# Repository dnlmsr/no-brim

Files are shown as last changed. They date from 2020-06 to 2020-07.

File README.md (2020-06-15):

# no-brim

## Descrizione
Il progetto no-brim (no Barbaric Resizing Is Mandatory) è il progetto di una macchina in grado di realizzare lunghezze di tubi in PVC o altri materiali plastici definite dall'utente. L'intero sistema è basato sulla piattaforma open source Arduino MEGA che gestisce tutti gli input e gli output e le interazioni con l'utente.
## Autori
* [Daniele Moser](mailto:dnlmsr0@gmail.com)
* [Francesco Maraner](mailto:francesco.maraner@marconirovereto.it)
* [Michele Mattè](mailto:michele.matte@marconirovereto.it)

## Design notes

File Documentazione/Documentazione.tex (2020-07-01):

\documentclass{report}
\usepackage[utf8]{inputenc}
\usepackage[italian]{babel}
\usepackage{amsmath}
\usepackage{graphicx}
\usepackage{float}
\usepackage{pdfpages}
\usepackage{siunitx}
\usepackage{caption}
\usepackage{subcaption}
\usepackage{tikz}
\usetikzlibrary{shapes,arrows}

\DeclareSIUnit{\rpm}{rpm}
\sisetup{range-phrase=\div}

\title{Progetto no-brim}
\author{Daniele Moser, Francesco Maraner, Michele Mattè}

\begin{document}
\maketitle
\tableofcontents

\chapter{Introduzione}
no-brim è il progetto di una segatrice per tubi in PVC o altri materiali plastici, creato per il corso di Alta Formazione Professionale. Alla base di questo progetto, è presente la progettazione meccanica, elettronica e di programmazione di un macchinario semiautomatico per il taglio di lunghezza variabile di tubi mediante una discreta varietà di componenti (motori elettrici, assi, pistoni pneumatici, elettrovalvole, trasmissione a cinghia e lama circolare) che operano simultaneamente per realizzare il prodotto finale. Le motivazioni che ci hanno proiettato su questa tipologia di progetto derivano dal desiderio di mettere in atto le nozioni apprese durante il primo e secondo praticantato, dove ognuno dei 3 componenti del gruppo ha avuto modo di confrontarsi con il mondo del lavoro e di migliorare e accrescere le sue conoscenze nei vari ambiti in cui ha potuto lavorare, come la creazione di sistemi di trasmissione del moto o la programmazione.
\chapter{Meccanica}

\section{Descrizione macchina e motivazione dei componenti}
La parte meccanica, realizzata su Inventor, è stata divisa in 2 gruppi principali:
\begin{itemize}
\item Trasporto;
\item Taglio ed espulsione.
\end{itemize}

\subsection{Trasporto}
\begin{figure}[H]
  \centering
  \begin{subfigure}[H]{0.45\textwidth}
    \centering
    
  \end{subfigure}
  \hfill
  \begin{subfigure}[H]{0.45\textwidth}
    \centering
    
    \end{subfigure}
    \caption{Gruppo trasporto}
    \label{fig:vtcons}
\end{figure}
La prima parte si occupa del trasporto del tubo mediante un asse lineare ($l=\SI{300}{\mm}$) che sfrutta una trasmissione a vite a ricircolo di sfere, comandata da un motore elettrico, per spostare un pistone pneumatico (1M1), dove alla sua estremità è montata una lamiera che con la sua elasticità garantisce la corretta aderenza al tubo, sfruttando tutta la forza del pistone. Il pistone è stato collegato al pattino dell’asse lineare mediante una lamiera e una piastra. Dalla parte opposta all’asse, troviamo una lamiera a forma di “V” che garantisce il corretto scorrimento del tubo fino alla parte di taglio, grazie all’utilizzo di una rulliera costruita con dei cuscinetti a sfera.
Poco più a destra dell’asse lineare si colloca un altro pistone (2M1) fisso a telaio che si occupa di bloccare il tubo con la stessa logica del primo, contro un supporto in materiale tenero per non danneggiare l’oggetto da lavorare.
\begin{figure}[H]
  \centering
  
  \caption{Pistone bloccaggio}
  \label{fig:pinzaggio}
\end{figure}
All’estremità del telaio sono presenti delle lamiere che garantiscono il corretto ingresso ed uscita del tubo dalla parte di trasporto e dei sensori per controllare la posizione di quest’ultimo. Il telaio è stato realizzato mediante l’uso di tubolari quadrati in acciaio, dove sono stati fissati i supporti per le parti nominate in precedenza.

\subsection{Taglio ed espulsione}
\begin{figure}[H]
  \centering
  \begin{subfigure}[H]{0.45\textwidth}
    \centering
    
  \end{subfigure}
  \hfill
  \begin{subfigure}[H]{0.45\textwidth}
    \centering
    
    \end{subfigure}
    \caption{Gruppo taglio}
    \label{fig:vtcons}
\end{figure}
La seconda parte si occupa del taglio e l’espulsione del tubo mediante l’uso di una sega circolare ($D=\SI{300}{\mm}$) messa in moto da un motore elettrico monofase ($P = \SI{1,5}{\kW}$, $n_{max}=\SI{2500}{\rpm}$), il tutto collegato con una trasmissione a cinghie piatte con rapporto di trasmissione $i=\num{0.5}$ che si occupa di moltiplicare i giri della puleggia operatrice per garantire un taglio ottimale, come consigliato da tabella. Il sotto-assieme descritto è stato assemblato con un “telaietto” creato con dei tubolari quadrati in acciaio di piccole dimensioni per contenere il peso complessivo (motore, trasmissione, porta cuscinetto e lama) e vincolato ad un’estremità con 2 perni (che generano un effetto cerniera) che permettono la salita e la discesa di quest’ultimo mediante un pistone a doppio effetto (3MX). Per trasformare lo spostamento lineare del pistone in angolare dovuto alla rotazione attorno ai perni sono stati montati dei perni a forcella, collocati tra una piastra fissa e la base del pistone e tra l’estremità dello stelo e il telaietto, garantendo una buona spinta senza considerevoli perdite di forze. 

Infine, troviamo l’espulsione del pezzo lavorato grazie all’utilizzo di un pistone pneumatico (4M1) dove all’estremità dello stelo è stata fissata una lamiera con delle prolunghe laterali che fanno scorrere il tubo su un piano d’appoggio (con la possibilità di essere allungato in base alla lunghezza del tubo desiderata) verso una caduta libera.
\begin{figure}[H]
  \centering
  
  \caption{Pistone espulsione}
  \label{fig:espulsione}
\end{figure}
Il telaio portante è stato realizzato mediante l’uso di tubolari quadrati in acciaio, dove sono stati fissati i supporti per le parti nominate in precedenza.

\section{Calcoli di progetto}
\subsection{Calcolo dei giri utili del motore}
I tubi da tagliare, utilizzati per il trasporto di fluidi possono esseri creati con 3 diversi materiali plastici:
\begin{itemize}
\item PVC (cloruro di polivinile) con	$R_m = \SI{55}{\MPa}$;
\item PVC-C $R_m = \SI{60}{\MPa}$;
\item PE (polietilene) $R_m = \SI{17}{\MPa}$;
\item PP (polipropilene) $R_m = \SI{35}{\MPa}$.
\end{itemize}
PVC, PE e PP fanno parte della famiglia dei pannelli termoplastici (tabella $V_t$ consigliate) dove la velocità di taglio $V_t$ consigliata si aggira tra $\SIrange{50}{75}{\m\per\s}$ e l’avanzamento tra $\SIrange{0.05}{0.1}{\mm\per\s}$.

\begin{figure}[H]
    \centering
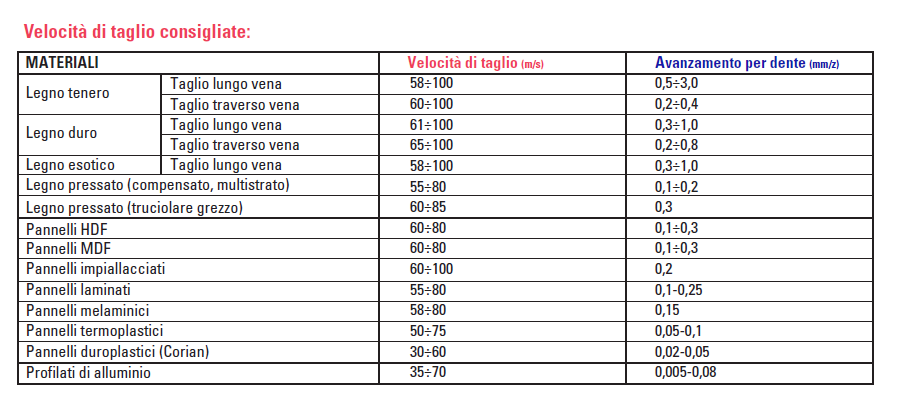
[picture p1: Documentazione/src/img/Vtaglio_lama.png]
    
    \caption{$V_t$ consigliate}
    \label{fig:vtcons}
\end{figure}

Seguendo la linea nera (per materiali plastici) della tabella, si assume un diametro della lama circolare di $D=\SI{300}{\mm}$ (inoltre utilizzata nella maggior parte dei casi, grazie al suo ottimo rapporto efficienza/ingombro).

\begin{figure}[H]
    \centering
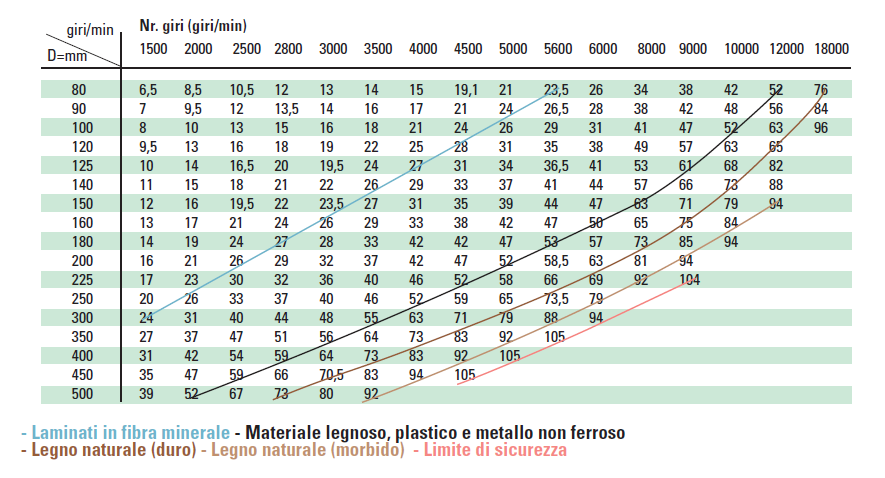
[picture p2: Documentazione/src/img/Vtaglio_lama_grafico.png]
    
    \caption{Grafico $V_t$ consigliate}
    \label{fig:grafvtcons}
\end{figure}

Conoscendo la $V_t$ richiesta dal materiale per essere tagliato possiamo calcolare il numero di giri generati dal motore, che successivamente verranno moltiplicati mediante una trasmissione a cinghie piatte.
Sapendo che:
\begin{equation}
  \omega=\frac{V_t}{r_{lama}}
\end{equation}
Si calcola:
\begin{itemize}
\item $\omega_{min} = \frac{V_t}{r} = \frac{\SI{50}{\m\per\s}}{\SI{0,15}{\m}} = \SI{334}{\radian\per\s} $;
\item $\omega_{max}  = \frac{V_t}{r}= \frac{75}{0,15} = \SI{500}{\radian\per\s}$.
\end{itemize}

Per una lettura più comoda si converte la $\omega$ in rpm mediante la seguente formula:
\begin{equation}
  n = \frac{60\omega}{2\pi}
\end{equation}

Quindi:
\begin{description}
\item $n_{min} = \frac{334\cdot 60}{2\pi} \approx \SI{3200}{\rpm}$;
\item $n_{max} = \frac{500\cdot 60}{2\pi} \approx \SI{4800}{\rpm}$.
\end{description}

Conoscendo questi dati, con l’intenzione di utilizzare una trasmissione a cinghie piatte con un rapporto di trasmissione $i = \num{0,5}$ (che moltiplica la velocità della puleggia operatrice del doppio rispetto a quella motrice) si può restringere il campo di ricerca del motore monofase fino a \SI{2500}{\rpm} massimi che, grazie alla trasmissione, potrà raggiungere i \SI{5000}{\rpm}.

\subsection{Calcolo della forza di taglio}
La taglia del tubo da tagliare, nel nostro caso, ha le seguenti dimensioni:
\begin{description}
\item $D = \SI{104}{\mm}$
\item $d = \SI{100}{\mm}$
\item $A = \SI{641}{\mm\squared}$
\end{description}

Utilizzando il carico di rottura del materiale più resistente (PVC-C) con $\sigma = \SI{60}{\MPa}$, si calcola la sua $\tau$, sapendo che $\tau = \frac{\sigma}{\sqrt{3}}$ e di conseguenza $\tau = k\frac{F}{A}$ dove per sezioni circolari $k=4/3$. Rovesciando la formula si può calcolare la $F$ necessaria per tagliare il tubo:

\begin{equation}
\tau=\frac{60}{\sqrt{3}} = \SI{35}{\MPa}
\end{equation}
\begin{equation}
F = \frac{A\tau}{k} = \SI{16,7}{\kN}
\end{equation}

\subsection{Calcolo della potenza del motore}
Per il calcolo della potenza del motore, dopo aver trovato il numero di giri necessari, è stato utilizzato il metodo sperimentale. Grazie alla presenza di una sega circolare (da falegnameria) e il tubo da lavorare, dopo varie prove e tagli siamo giunti alla conclusione di adottare un motore con una potenza di \SI{1,5}{\kW}. La possibilità di provare il taglio ci ha permesso di stabilire le seguenti considerazioni:
\begin{itemize}
\item Le velocità di taglio, calcolate in precedenza sono state del tutto coerenti con le prove effettuate.
\item La velocità di avanzamento, invece, ha soddisfatto le aspettative con un andamento lento e costante, senza imprimere troppa forza (circa \SI{50}{\N}) tra il tubo e la lama per evitare che quest'ultima si bloccasse.
  \end{itemize}
  \subsection{Dimensionamento della trasmissione}
  \begin{figure}[H]
    \centering
    \begin{subfigure}[H]{0.45\textwidth}
    \centering
    
  \end{subfigure}
  \hfill
  \begin{subfigure}[H]{0.45\textwidth}
    \centering
    
    \end{subfigure}
    \caption{Gruppo trasmissione}
    \label{fig:vtcons}
\end{figure}
Le cinghie sono organi flessibili impiegati nella trasmissione di potenza da una puleggia motrice a una condotta, montate su alberi disposti ad una certa distanza (interasse). Le cinghie possono appartenere a due gruppi distinti: cinghie di tipo convenzionale e cinghie sincrone.
Le cinghie di tipo convenzionale trasmettono il moto sfruttando l’aderenza (attrito) con il profilo esterno della puleggia. In questo caso possono verificarsi scorrimenti fra la cinghia e la puleggia durante il moto.
Le cinghie sincrone trasmettono il moto tramite l’ingranamento dei denti della cinghia con quelli della puleggia. Non sono soggette a scorrimento e necessitano di un precarico molto modesto.
Industrialmente sono usate cinghie piatte, trapezoidali e sincrone.
Per dimensionare una trasmissione partiamo dai dati del motore, forniti dal datasheet:

\begin{table}[H]
\centering
\begin{tabular}{|l|c|}
\hline
\multicolumn{2}{|c|}{\textbf{Dati motore}} \\ \hline
Potenza & \SI{1,5}{\kW} \\ \hline
Giri motore & \SI{2500}{\rpm} \\ \hline
Diametro albero & \SI{19}{\mm} \\ \hline
\end{tabular}
\end{table}

Successivamente, una volta trovato il numero di giri che vogliamo sviluppare sull’operatrice ($n=\SI{5000}{\rpm}$), calcolo il rapporto di trasmissione ($i$) e l’interasse ($I$) tra i due elementi rotanti in base alla dimensione delle mie pulegge, che assumo a piacere dalla serie di Renard R20 a partire da un diametro minimo di \SI{40}{\mm}.

Assumiamo il diametro della puleggia motrice $D_m=\SI{100}{\mm}$ e di conseguenza (per rispettare il rapporto di trasmissione e la serie R20) $D_o=\SI{50}{\mm}$ per il diametro dell’operatrice. Questa scelta è giustificata dagli ingombri in fase di modellazione 3D per tagliare correttamente il tubo senza urti.
Il calcolo dell’interasse dipende dal carico, nel nostro caso $I\geq 3\cdot D_m$ per trasmissioni a carico variabile. Una volta rispettata questa condizione si può scegliere a piacimento la lunghezza in base alle esigenze (ingombri, etc...)

\begin{table}[H]
\centering
\resizebox{\textwidth}{!}{
\begin{tabular}{|l|c|l|}
\hline
\multicolumn{2}{|c|}{\textbf{Dati Pulegge}} & \multicolumn{1}{c|}{\textbf{Formula}} \\ \hline
Numero giri motrice ($n_m$) & \SI{2500}{\rpm} & Fornito dal motore \\ \hline
Numero giri operatrice ($n_o$) & \SI{5000}{\rpm} & $\frac{n_m}{i}$ \\ \hline
Rapporto di trasmissione ($i$) & \num{0,5} & $\frac{n_m}{n_o}$ \\ \hline
Diametro puleggia motrice ($D_m$) & \SI{100}{\mm} & Scelta personale rispettando R20 \\ \hline
Diametro puleggia operatrice ($D_o$) & \SI{50}{\mm} & $D_o=D_m\cdot i$ \\ \hline
Interasse ($I$) & \SI{300}{\mm} & $I=3\cdot D_m$ \\ \hline
\end{tabular}
}
\end{table}

Durante la progettazione di una trasmissione è importante consultare le tabelle unificate che forniscono dati di correzione in base ai materiali utilizzati per la realizzazione e il servizio che devono compiere.
Dati provenienti dalle tabelle del manuale di Meccanica:
\begin{table}[H]
\centering
\begin{tabular}{|c|c|l|}
\hline
\multicolumn{2}{|c|}{\textbf{Dati tabelle}} & \multicolumn{1}{c|}{\textbf{Provenienza dati}} \\ \hline
$F_s$ & \num{1,2} & Tab. I.101 Fattore di servizio \\ \hline
$F_t$ & \num{1} & Tab. I.102 Fattore correttivo \\ \hline
$F_\alpha$ & \num{1} & Tab. I.108 Coeff. correzione \\ \hline
$P_1$ & \num{0,7} & Tab. I.106 P specifica (cinghia gomma-tessile) \\ \hline
\end{tabular}
\end{table}

\subsubsection{Calcolo della potenza corretta}
\begin{equation}
P_c=P\cdot F_s\cdot F_t
\end{equation}
Dove $P$ è la potenza erogata dal motore, $F_s=\num{1,2}$ da tabella per macchine utensili che lavorano dalle 8 alle 10 ore al giorno e $F_t=1$ da tabella per condizioni normali.
\begin{equation}
P_c = \SI{1,5}{\kW}\cdot \num{1,2}\cdot 1 = \SI{1,8}{\kW}
\end{equation}
\subsection{Calcolo della velocità periferica della puleggia minore}
\begin{equation}
  V = \frac{\pi D_{min}n_{min}}{\num{60000}}
\end{equation}
Dove $D_{min}=D_o$ e $n_{min}=n_o$.
\begin{equation}
V=\frac{\pi\cdot 50\cdot 5000}{\num{60000}} = \SI{13,1}{\m\per\s}
\end{equation}

\subsubsection{Calcolo della lunghezza della cinghia}
\begin{equation}
  l=2I+\frac{\pi (D_m+D_o)}{2}+\frac{(D_o-D_m)^2}{4I}=\SI{838}{\mm}\approx\SI{840}{\mm}
\end{equation}
Si approssima a \SI{840}{\mm} per lasciare un po' di gioco prima di tendere o allentare la cinghia.

\subsubsection{Calcolo dell’angolo di avvolgimento $\alpha$}
\begin{equation}
  \alpha = \SI{180}{\degree}-\SI{57}{\degree}\cdot\frac{D_m-D_o}{I}=\SI{190}{\degree}
\end{equation}
Il valore servirà per trovare $F\alpha$ da tabella.
\subsubsection{Calcolo della larghezza della cinghia $a$}
I principali materiali utilizzati per la costruzione di cinghie piatte sono:
\begin{itemize}
\item cuoio;
\item struttura composita di laminati plastici e gomme o resine;
\item struttura composita di gomme e tessili;
\item cotone, balata e altre fibre tessili vegetali;
\item gomma o materiali plastici (per alte velocità).
\end{itemize}
Da questa informazione si può calcolare la larghezza della cinghia ricavando il valore $P_1$ in base al materiale scelto, nel nostro caso gomma-tessile pesante in cotone a 4 tele, data la seguente formula:
\begin{equation}
  a = \frac{P_c}{P_1F_\alpha}=\frac{\SI{1,8}{\cm}}{\SI{0,7}{\cm}\cdot 1} = \SI{2,57}{\cm}\approx\SI{26}{\mm}
\end{equation}
La larghezza della cinghia è stata scelta in riferimento ai valori dati dalla serie R40, a partire dal valore minimo di 16 mm.

\subsubsection{Calcolo dello spessore della cinghia $s$}
Dalla seguente tabella ricavo lo spessore $s$ della cinghia in base al materiale scelto in precedenza. In questo caso \SI{6}{\mm}.
\begin{table}[H]
\resizebox{\textwidth}{!}{%
\begin{tabular}{|c|c|c|c|c|}
\hline
\multicolumn{5}{|c|}{\textbf{Campo applicazione per cinghie piatte}} \\ \hline
\textit{\textbf{\begin{tabular}[c]{@{}c@{}}Tipo di cinghia \\ e materiale\end{tabular}}} & \textit{\textbf{Costruzione}} & \textit{\textbf{\begin{tabular}[c]{@{}c@{}}Potenza Max \\ $[\si{\kW}]$\end{tabular}}} & \textit{\textbf{\begin{tabular}[c]{@{}c@{}}Velocità Max \\ $[\si{\m\per\s}]$\end{tabular}}} & \textit{\textbf{\begin{tabular}[c]{@{}c@{}}Spessore cinghia s \\ $[\si{\mm}]$\end{tabular}}} \\ \hline
Cuoio & \begin{tabular}[c]{@{}c@{}}- Semplice\\ - Doppia\\ - Triplice\end{tabular} & \begin{tabular}[c]{@{}c@{}}750\\ 500\\ 1500\end{tabular} & \begin{tabular}[c]{@{}c@{}}40\\ 30\\ 25\end{tabular} & \begin{tabular}[c]{@{}c@{}}4 - 6\\ 7 - 9\\ 11 - 14\end{tabular} \\ \hline
\begin{tabular}[c]{@{}c@{}}Componente:\\ - Nylon\\ - Poliestere\end{tabular} & \begin{tabular}[c]{@{}c@{}}- Lamina in gomma\\ - Plastici\end{tabular} & 3500 & 40 & 0,5 - 6 \\ \hline
\begin{tabular}[c]{@{}c@{}}Composita:\\ - Gomma\\ - Tessile\end{tabular} & \begin{tabular}[c]{@{}c@{}}- Tessuti medi\\ - Tessuti pesanti\end{tabular} & \begin{tabular}[c]{@{}c@{}}750\\ 1500\end{tabular} & \begin{tabular}[c]{@{}c@{}}40\\ 40\end{tabular} & \begin{tabular}[c]{@{}c@{}}6 - 20\\ 6 - 20\end{tabular} \\ \hline
  \begin{tabular}[c]{@{}c@{}}Cotone, balata \\ e altre fibre tessili\end{tabular} & \begin{tabular}[c]{@{}c@{}}- Multistrato\\ - Unico strato\end{tabular} & 1500 & 30 & 4 -
                                                                                                                                                                         20 \\ \hline
\begin{tabular}[c]{@{}c@{}}In gomma e plastici \\ per alte velocità\end{tabular} & - Unico strato & 50 & 70 & 0,5 - 2 \\ \hline
\end{tabular}%
}
\caption{Parametri consigliati per vari tipi di cinghie}
\end{table}
\subsubsection{Calcolo della larghezza della puleggia $b$}
\begin{equation}
  b = \num{1,15}\cdot a\approx\SI{30}{\mm}
\end{equation}
\subsubsection{Calcolo della bombatura della puleggia $h$}
Le pulegge per cinghie piatte vengono costruite con profilo esterno leggermente bombato per ottenere la stabilità della cinghia sulla corona. I materiali più indicati sono l’alluminio, per il peso contenuto, o la ghisa per piccole serie.
\begin{equation}
 h=\num{0,006}\cdot b=\SI{0.186}{\mm}
\end{equation}
\section{Schema elettro-pneumatico}
\subsection{Scelta dei componenti}
Lo schema elettro-pneumatico è stato realizzato con i seguenti componenti:
\begin{description}
\item[Compressore] Si occupa di accumulare e innalzare la pressione dell’aria all’interno del suo serbatoio per alimentare il circuito pneumatico;
\item[Gruppo trattamento aria] Composta da filtro di scarico manuale, un riduttore di pressione variabile, un manometro e una valvola di sicurezza (quasi sempre inclusa nei gruppi trattamento aria industriali per togliere aria al sistema in caso di emergenza);
\item[Pistone pinza mobile 1M1, pistone pinza fissa 2M1, pistone espulsore 4M1] Composti dalla stessa logica, tramite l'uso di:
  \begin{itemize}
  \item 1 pistone a singolo effetto con ritorno a molla con le seguenti caratteristiche: corsa di \SI{50}{\mm}, diametro pistone \SI{16}{\mm} e forza di spinta teorica a $\SI{6}{\bar}$ di $F=\SIrange{90}{120}{\bar}$ (dove la sola andata è utile per svolgere il lavoro richiesto di bloccaggio ed espulsione);
  \item 1 strozzatore che si utilizza solamente uno strozzatore senza una o più valvole di non ritorno perché la regolazione della portata mediante strozzatura su ambedue i lati viene spesso applicata in cilindri a semplice effetto o in cilindri di piccole dimensioni che svolgono lavori “semplici”. Quest’aspetto inoltre va a vantaggio dei costi di realizzazione dell’impianto e della semplicità d’applicazione;
  \item 1 valvola 3/2 normalmente chiusa comandata elettricamente nella fase di spinta e con ritorno a molla;
  \end{itemize}
\item[Pistone sollevamento lama circolare 3MX] Composto da:
  \begin{itemize}
  \item 1 pistone a doppio effetto con le seguenti caratteristiche: corsa \SI{100}{\mm}, diametro del pistone \SI{32}{\mm} e forza di spinta teorica a \SI{6}{\bar} di $F=\SIrange{415}{483}{\N}$, dati necessari a soddisfare il corretto movimento della lama verso l'alto, considerando che il peso che deve movimentare è composto dal telaietto con relativa trasmissione (motore, cinghia, pulegge etc) che risulta essere circa \SI{25}{\kg}, di conseguenza \SI{250}{\N} con un ulteriore aggiunta di \SI{50}{\N} per la fase di avanzamento come descritto nei calcoli. In questo modo, con una determinata forza richiesta ($F=\SI{300}{\N}$) è stato scelto un pistone leggermente sovradimensionato per tenere conto delle possibili piccole perdite di forza dovute agli attriti dei perni a forcella;
  \item 2 strozzatori in scarico per ottenere una buona regolazione della portata, entro certi limiti indipendenti dal carico applicato allo stelo, poiché viene guidato dal cuscino d’aria che si forma nella camera di scarico; agendo sulle viti di regolazione degli strozzatori si possono tarare separatamente le velocità delle due corse.
  \item 1 valvola 5/3 a centri chiusi comandata elettricamente con ritorno a molla in ambedue i versi di commutazione per comandare il pistone a doppio effetto. La scelta di questa valvola è dovuta alla necessità di mantenere in posizione la lama (senza spostarsi in punti indesiderate, evitando danni all’oggetto da tagliare) in caso di arresto voluto o improvviso.
  \end{itemize}

\item[Finecorsa dei pistoni] Festo prevede l’utilizzo di sensori magneti che determinano la corsa dello stelo, montati direttamente sul cilindro.
\end{description}

\subsection{Lista componenti}
\begin{table}[H]
\centering
\begin{tabular}{|l|c|}
  \hline
  {\textbf{Componenti}} & \textbf{Quantità} \\ \hline
  Pistone singolo effetto & 3 \\ \hline
  Pistone doppio effetto & 1 \\ \hline
  Elettrovalvola 3/2 nc con ritorno a molla & 3 \\ \hline
  Elettrovalvola 5/3 centri chiusi con ritorno a molla & 1 \\ \hline
  Strozzatori & 5 \\ \hline
  Valvole di non ritorno & 2 \\ \hline
  Gruppo trattamento aria & 1 \\ \hline
  Compressore & 1 \\ \hline
\end{tabular}
\end{table}

\chapter{Elettronica}

\section{Descrizione circuiti e motivazione dei componenti}
La parte elettronica, realizzata utilizzando KiCad e DesignSpark Eletrical, è stata suddivisa in 2 parti separate:
\begin{itemize}
\item PCB
\item Quadro
\end{itemize}
\section{PCB}
La prima parte è costituita da una serie di circuiti che permettono ad Arduino di comandare 4 elettrovalvole e due motori rispettivamente da 24V e da 230V. Nel caso specifico viene inserito tra l'output di Arduino e l'elettrovalvola, un MOSFET che fungerà da interruttore per alimentare e disalimentare l'elettrovalvola in questione o il motore.
\begin{figure}[H]
  \centering
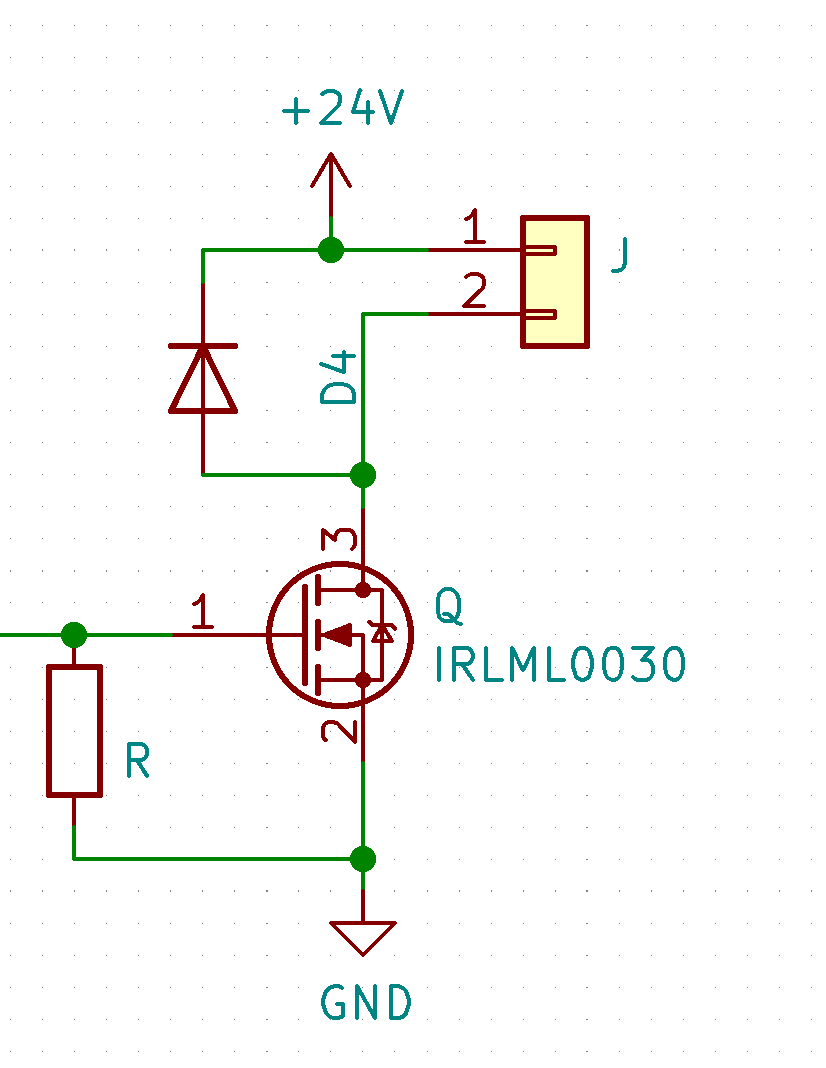
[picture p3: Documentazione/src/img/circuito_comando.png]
  
  \caption{Circuito di comando}
  \label{fig:circuito}
\end{figure}
Per quanto riguarda le dimensioni del circuito stampato risultano contenute nonostante la quantità di dispositivi ad esso collegati, infatti il circuito integra solamente la parte composta da una morsettiera con 10 connettori, dedicati ad ognuno degli ingressi necessari, i circuiti di comando e i morsetti di uscita. Ogni circuito di comando è composto un MOSFET e un diodo: 
\begin{description}
\item[Diodo] La funzione del diodo in questo circuito è quella di proteggere il MOSFET e l'uscita di Arduino da sovratensioni indesiderate provocate dagli avvolgimenti presenti nelle elettrovalvole e nei motori, in alcuni casi viene inserito anche per evitare le inversioni di tensione. Per quanto riguarda il circuito di comando per il motore della lama monofase $\SI{230}{\volt}$, utilizzato per la sega, si è preferito introdurre anche un relè così da permettere di utilizzare un MOSFET con corrente di sollecitazione minore e ridurre la tensione massima presente sulla scheda da $\SI{230}{\volt}$ AC a $\SI{24}{\volt}$ DC.
\item[MOSFET] È il cuore del circuito infatti, grazie ad una piccola sollecitazione ($\SIrange{0}{10}{\milli\ampere}$) riesce a veicolare correnti di valore molto più alte ($\SIrange{1}{7}{\ampere}$), nel nostro caso le correnti non superano normalmente i $\SI{2}{\ampere}$ quindi, date le correnti basse non necessitano della presenza di alette di raffreddamento. Per quanto riguarda invece il motore responsabile della movimentazione dell'asse lineare necessita di $\SI{7,7}{\ampere}$ come corrente di spunto.
\end{description}
\section{Quadro}
La seconda parte del circuito è racchiusa in un quadretto di modeste dimensioni al quale viene data in ingresso una tensione monofase $\SI{230}{\volt}$ e in uscita due tensioni continue dal valore di $\SI{24}{\volt}$ e $\SI{12}{\volt}$.
Per permettere la conversione in tensione continua sono stati creati due circuiti di trasformazione separati e provvisti di interruttori magnetotermici differenziali per garantire la sicurezza elettrica del quadro.
Il quadretto in questione verrà in seguito collegato al connettore di terra dello stabilimento.
\section{Descrizione della componentistica}
Sono stati utilizzati i seguenti componenti:
\begin{itemize}
\item Motore dell'asse lineare: un motore brushless di Pamoco con dati di targa di $\SI{24}{\volt}$ e corrente di spunto di $\SI{7,7}{\ampere}$;
\item Motore della sega circolare: un motore di Bonfiglioli con dati di targa di $\SI{230}{\volt}$ monofase e corrente di spunto di $\SI{2,4}{\ampere}$;;
\item Elettrovalvola 4/2 di Fluidmec con pilotaggio elettrico su entrambi i lati con dati di targa di $\SI{24}{\volt}$ e corrente di spunto di $\SI{0,8}{\ampere}$; 
\item Elettrovalvola 5/3 di Festo a centri chiusi con pilotaggio elettrico su entrambi i lati con dati di targa di $\SI{24}{\volt}$ e corrente di spunto di $\SI{0,5}{\ampere}$;
\item Elettrovalvola 3/2 di Schmieranlagen con pilotaggio elettrico a sinistra e ritorno a molla a destra con dati di targa di $\SI{24}{\volt}$ e corrente di spunto di $\SI{0,8}{\ampere}$;
\end{itemize} 

\chapter{Programmazione}
\section{Programma Arduino}
L'intero sistema è basato sulla piattaforma open source \emph{Arduino MEGA}, la quale gestisce l'intero funzionamento del sistema. Il programma che gira su Arduino è basato su un sistema a task e scheduler, ciò vuol dire che l'intero programma è suddiviso in piccoli sottoprogrammi (task) che vengono eseguiti ad una certa frequenza predefinita dallo scheduler il quale compito è appunto quello di eseguire questi programmi al momento giusto. Il programma dispone anche di un sistema per verificare se il sistema è real-time, ovvero che la capacità di calcolo del microcontrollore sia adeguata alla mole di calcoli richiesti dal programma. Questo sistema verifica appunto la saturazione della CPU.
\subsection{SFC}
Il programma per la movimentazione viene eseguito da un task adibito al corretto funzionamento dove si è cercato di replicare un sistema a stati.
\begin{enumerate}
\item Stato di STOP;
\item Tutte le movimentazioni vengono calibrate, quindi tutti i pistoni tranne 2M1 vengono resettati e l'asse lineare si sposta nella posizione più lontana dalla lama;
\item Viene pinzato il tubo con il pistone 1M1;
\item Viene resettato il pistone 2M1 e l'asse lineare si sposta in avanti verso la lama. Se la lunghezza del tubo non è soddisfatta si torna al punto 2;
\item Il tubo viene pinzato con il pistone 2M1;
\item Viene accesa la lama e viene effettuato il taglio con 3M1;
\item Viene fermata la lama e viene retratto il blocco di taglio con 3M2;
\item Viene espulso il pezzo finito e si torna allo stato di calibrazione.
\end{enumerate}
\section{Sistema asse lineare}
È stato deciso di studiare in profondità il funzionamento dell'asse lineare per poter tarare con maggior accuratezza il controllore. È quindi necessario conoscere le specifiche sia del motore che dell'asse lineare:
\begin{table}[H]
\centering
\begin{tabular}{|l|c|c|}
  \hline
\textbf{Descrizione}    & \textbf{Sigla} & \textbf{Valore}   \\ \hline
  \multicolumn{3}{|c|}{\textbf{Dati Motore}}                                                               \\ \hline

Corrente di spunto      & $i_s$                              & \SI{7,7}{\ampere}                       \\ \hline
Tensione nominale       & $v_n$                              & \SI{24}{\volt}                          \\ \hline
Velocità motore a vuoto & $\omega_{n}$                       & \SI{3500}{\rpm}                          \\ \hline
\multicolumn{3}{|c|}{\textbf{Dati asse lineare}}                                                         \\ \hline
Momento di inerzia      & $J$                                & \SI{0,11}{\kg\cm\squared\per\m} \\ \hline
Passo vite              & $p$                                & \SI{5}{\mm}                         \\  \hline
\end{tabular}
\end{table}
È necessario inoltre calcolare la resistenza di armatura e la costante elettrica e meccanica del motore:
\begin{equation}
  R_a=\frac{v_n}{i_s}=\SI{3,12}{\ohm}
\end{equation}
\begin{equation}
  K=\frac{v_n}{\omega_n}=\SI{6,86}{\milli\volt\per\rpm}
\end{equation}
\subsection{Sistema motore}
Per poter studiare il motore si fa uso delle formule del motore in corrente continua:
\begin{equation}
  \begin{cases}
    Ri(t)+K\omega(t)=V(t)\\
    J\dot \omega(t)=Ki(t)
  \end{cases}
\end{equation}
Si decide quindi di portare l'intero sistema nel dominio di Laplace:
\begin{equation}
  \begin{cases}
    RI(s)+K\omega(s)=V(s)\\
    Js\omega(s)=KI(s)    
  \end{cases}
\end{equation}
Eliminando $I(s)$ si ottiene:
\begin{equation}
  \frac{Js\omega(s)}{K}=\frac{V(s)-K\omega(s)}{R}\longrightarrow\frac{\omega(s)}{V(s)}=\frac{K}{JsR+K^2}
\end{equation}
\subsection{Sistema completo}
Dopo aver trovato la funzione che descrive il funzionamento del motore CC è necessario anche descrivere il funzionamento del controllore. Nel nostro caso è stato utilizzato un controllore PID. Lo schema a blocchi rappresenta il sistema completo:
\begin{figure}[H]
  \centering
  \begin{tikzpicture}[auto, node distance=3cm,>=latex']
    \tikzstyle{block} = [draw, rectangle, 
    minimum height=3em, minimum width=6em]
    \tikzstyle{sum} = [draw, circle, node distance=1cm]
    \tikzstyle{input} = [coordinate, node distance=1cm]
    \tikzstyle{output} = [coordinate, node distance=2cm]
    \tikzstyle{pinstyle} = [pin edge={to-,thin,black}]
    
    \node [input, name=input] {};
    \node [sum, right of=input] (sum){};
    \node [block, right of=sum] (controller) {Controller};
    \node [block, right of=controller] (motore) {Motore};
    \node [block, right of=motore] (conversione) {Conversione};
    \node [output, right of=conversione] (output) {};

    \draw [draw,->] (input) -- node {$S_p$} (sum);
    \draw [->] (sum) -- node {$e$} (controller);
    \draw [->] (controller) -- (motore);
    \draw [->] (motore) -- (conversione);
    \draw [->] (conversione) -- node [name=y] {$y$}(output);
    \draw [->] (y) |- (5,-2) -| (sum);
    \node [below left] at (sum) {$-$};
  \end{tikzpicture}
\end{figure}
A questo punto avendo la descrizione del sistema completo si è deciso di simulare l'intero sistema tramite l'utilizzo di Octave. Il risultato sottostante si è ottenuto con $K_P=2$ e $K_I=K_D=0$.
\begin{figure}[H]
  \centering
  
  \caption{Simulazione asse lineare}
  \label{fig:simulazione}
\end{figure}
Tarando quindi i giusti valori di PID è possibile ottenere un sistema teoricamente ottimale, ma che richiede comunque una prova sperimentale sul campo.

\chapter{Sviluppi futuri}
\section{Sviluppi ambito elettronico}
  Uno sviluppo futuro per questo progetto consisterebbe nella progettazione e realizzazione di un circuito di sicurezza implementando barriere o cancelli che impediscano agli operatori di infortunarsi a causa delle diverse parti in movimento presenti nel macchinario.

\section{Sviluppi ambito programmazione} 
Sono da implementare l'interfacciamento con l'utente tramite l'utilizzo di un encoder e di un display LCD, nonché la comunicazione seriale con un PC per effettuare un debugging del sistema se necessario. Un'implementazione futura potrebbe consistere nella creazione di un applicativo di visione, magari per il controllo della qualità la deformazione del tubo dopo il taglio.
  
\section{Sviluppi ambito meccanico}  
  Un altra possibile modifica al progetto potrebbe consistere nella creazione di un sistema mobile per quanto riguarda la struttura contenente la sega circolare così da permettere anche quest'ultima di muoversi al posto della sola movimentazione del tubo, ottimizzando così le tempistiche dedicate al taglio.
  Un possibile miglioramento futuro, riferito alla parte meccanica, potrebbe consistere nell’utilizzo di una struttura verticale con la lamiera di supporto per lo scorrimento del tubo a forma di “V”, con relativa rulliera e i pistoni 1M1 e 2M1 (che utilizzano lo stesso sistema di trasporto) disposti al di sopra di quest’ultima. Per la parte di taglio, invece, si pensava di effettuare il taglio mediante una lama circolare calettata ad un piccolo motore elettrico, il tutto fissato a delle piastre montate su un corsoio con relative sicurezze, per movimentare agevolmente un peso contenuto in orizzontale; ed infine per la parte di scarico una lamiera mobile che viene mossa da un pistone per rilasciare il pezzo finito lungo uno scivolo.

\chapter{Crediti}
\section{Software utilizzati}
\begin{description}
\item[Autodesk Inventor]Per la realizzazione e la rappresentazione dei pezzi meccanici
  \item[Fluidsim]Per la progettazione del sistema pneumatico
\item[KiCad]Per la progettazione del PCB
\item[Arduino]Per la programmazione del sistema
\item[Octave]Per la simulazione del sistema
\item[\LaTeX]Per la documentazione
\end{description}
\includepdf[pages=-,angle=90]{src/Tavole/completo.pdf}
\includepdf[pages=-,angle=90]{src/Tavole/trasporto.pdf}
\includepdf[pages=-,angle=90]{src/Tavole/taglio_1.pdf}
\includepdf[pages=-,angle=90]{src/Tavole/trasmissione.pdf}
\includepdf[pages=-]{src/img/impianto_elettropneumatico.pdf}
\end{document}

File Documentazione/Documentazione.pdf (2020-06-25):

# Progetto no-brim

Daniele Moser, Francesco Maraner, Michele Matt`e

25 giugno 2020

# Indice

1 Introduzione | 2
2 Meccanica | 3
2.2.5 | Calcolo della velocit`a periferica della puleggia minore . . | 8

1

# Capitolo 1

# Introduzione

2

# Capitolo 2

# Meccanica

## 2.1 Descrizione macchina e motivazione dei componenti

La parte meccanica, realizzata su Inventor, `e stata divisa in 2 gruppi principali:

- Trasporto;
- Taglio ed espulsione.

### 2.1.1 Trasporto

La prima parte si occupa del trasporto del tubo mediante un asse lineare (l = 300 mm) che sfrutta una trasmissione a vite a ricircolo di sfere, comandata da un motore elettrico, per spostare un pistone pneumatico (1M1), dove alla sua estremit`a `e montata una lamiera che con la sua elasticit`a garantisce la corretta aderenza al tubo, sfruttando tutta la forza del pistone. Il pistone `e stato collegato al pattino dell’asse lineare mediante una lamiera e una piastra. Dalla parte opposta all’asse, troviamo una lamiera a forma di “V” che garantisce il corretto scorrimento del tubo fino alla parte di taglio, grazie all’utilizzo di una rulliera costruita con dei cuscinetti a sfera. Poco pi`u a destra dell’asse lineare si colloca un altro pistone (2M1) fisso a telaio che si occupa di bloccare il tubo con la stessa logica del primo, contro un supporto in materiale tenero per non danneggiare l’oggetto da lavorare. All’estremit`a del telaio sono presenti delle lamiere che garantiscono il corretto ingresso ed uscita del tubo dalla parte di trasporto e dei sensori per controllare la posizione di quest’ultimo. Il telaio `e stato realizzato mediante l’uso di tubolari quadrati in acciaio, dove sono stati fissati i supporti per le parti nominate in precedenza.

3

### 2.1.2 Taglio ed espulsione

La seconda parte si occupa del taglio e l’espulsione del tubo mediante l’uso di una sega circolare (D = 300 mm) messa in moto da un motore elettrico monofase (P = 1.5 kW, nmax = 2500 rpm), il tutto collegato con una trasmissione a cinghie piatte con rapporto di trasmissione i = 0.5 che si occupa di moltiplicare i giri della puleggia operatrice per garantire un taglio ottimale, come consigliato da tabella. Il sottoassieme descritto `e stato assemblato con un “telaietto” creato con dei tubolari quadrati in acciaio di piccole dimensioni per contenere il peso complessivo (motore, trasmissione, porta cuscinetto e lama) e vincolato ad un’estremit`a con 2 perni (che generano un effetto cerniera) che permettono la salita e la discesa di quest’ultimo mediante un pistone a doppio effetto (3MX). Per trasformare lo spostamento lineare del pistone in angolare dovuto alla rotazione attorno ai perni sono stati montati dei perni a forcella, collocati tra una piastra fissa e la base del pistone e tra l’estremit`a dello stelo e il telaietto, garantendo una buona spinta senza considerevoli perdite di forze.
Infine, troviamo l’espulsione del pezzo lavorato grazie all’utilizzo di un pistone pneumatico (4M1) dove all’estremit`a dello stelo `e stata fissata una lamiera con delle prolunghe laterali che fanno scorrere il tubo su un piano d’appoggio (con la possibilit`a di essere allungato in base alla lunghezza del tubo desiderata) verso una caduta libera. Il telaio portante `e stato realizzato mediante l’uso di tubolari quadrati in acciaio, dove sono stati fissati i supporti per le parti nominate in precedenza.

## 2.2 Calcoli di progetto

### 2.2.1 Calcolo dei giri utili del motore

I tubi da tagliare, utilizzati per il trasporto di fluidi possono esseri creati con 3 diversi materiali plastici:

- PVC (cloruro di polivinile) con Rm = 55 MPa;
- PVC-C Rm = 60 MPa;
- PE (polietilene) Rm = 17 MPa;
- PP (polipropilene) Rm = 35 MPa.

PVC, PE e PP fanno parte della famiglia dei pannelli termoplastici (tabella Vt consigliate) dove la velocit`a di taglio Vt consigliata si aggira tra 50 m s⁻¹ ÷ 75 m s⁻¹

e l’avanzamento tra 0.05 mm s⁻¹ ÷ 0.1 mm s⁻¹

4


Figura 2.1: Vt consigliate

Seguendo la linea nera (per materiali plastici) della tabella, si assume un diametro della lama circolare di D = 300 mm (inoltre utilizzata nella maggior parte dei casi, grazie al suo ottimo rapporto efficienza/ingombro).


Figura 2.2: Grafico Vt consigliate

Conoscendo la Vt richiesta dal materiale per essere tagliato possiamo calcolare il numero di giri generati dal motore, che successivamente verranno moltiplicati mediante una trasmissione a cinghie piatte. Sapendo che:

ω =

Vt

rlama

(2.1)

Si calcola:

5

- ωmin =

Vt
r =

50 m s⁻¹
0.15 m = 334 rad s⁻¹
;
- ωmax =

Vt
r =

75

0,15 = 500 rad s⁻¹

Per una lettura pi`u comoda si converte la ω in rpm mediante la seguente formula:
n =

60ω
2π

(2.2)

Quindi:

nmin =

334·60
2π ≈ 3200 rpm;

nmax =

500·60
2π ≈ 4800 rpm.

Conoscendo questi dati, con l’intenzione di utilizzare una trasmissione a cinghie piatte con un rapporto di trasmissione i = 0.5 (che moltiplica la velocit`a della puleggia operatrice del doppio rispetto a quella motrice) si pu`o restringere il campo di ricerca del motore monofase fino a 2500 rpm massimi che, grazie alla trasmissione, potr`a raggiungere i 5000 rpm.

### 2.2.2 Calcolo della forza di taglio

La taglia del tubo da tagliare, nel nostro caso, ha le seguenti dimensioni:

D = 104 mm

d = 100 mm

A = 641 mm²

Utilizzando il carico di rottura del materiale pi`u resistente (PVC-C) con σ = 60 MPa, si calcola la sua τ , sapendo che τ = √σ
3

e di conseguenza τ = k

F
A
dove per sezioni circolari k = 4/3. Rovesciando la formula si pu`o calcolare la F necessaria per tagliare il tubo:

τ =

60
√
3
= 35 MPa | (2.3)

F =

Aτ
k
= 16.7 kN | (2.4)

### 2.2.3 Calcolo della potenza del motore

Per il calcolo della potenza del motore, dopo aver trovato il numero di giri necessari, `e stato utilizzato il metodo sperimentale. Grazie alla presenza di una sega circolare (da falegnameria) e il tubo da lavorare, dopo varie prove e tagli siamo giunti alla conclusione di adottare un motore con una potenza di 1.5 kW. La possibilit`a di provare il taglio ci ha permesso di stabilire le seguenti considerazioni:

6

- Le velocit`a di taglio, calcolate in precedenza sono state del tutto coerenti con le prove effettuate.
- La velocit`a di avanzamento, invece, ha soddisfatto le aspettative con un andamento lento e costante, senza imprimere troppa forza (circa 50 N) tra il tubo e la lama per evitare che quest’ultima si bloccasse.

### 2.2.4 Dimensionamento della trasmissione

Le cinghie sono organi flessibili impiegati nella trasmissione di potenza da una puleggia motrice a una condotta, montate su alberi disposti ad una certa distanza (interasse). Le cinghie possono appartenere a due gruppi distinti: cinghie di tipo convenzionale e cinghie sincrone. Le cinghie di tipo convenzionale trasmettono il moto sfruttando l’aderenza (attrito) con il profilo esterno della puleggia. In questo caso possono verificarsi scorrimenti fra la cinghia e la puleggia durante il moto. Le cinghie sincrone trasmettono il moto tramite l’ingranamento dei denti della cinghia con quelli della puleggia. Non sono soggette a scorrimento e necessitano di un precarico molto modesto. Industrialmente sono usate cinghie piatte, trapezoidali e sincrone. Per dimensionare una trasmissione partiamo dai dati del motore, forniti dal datasheet:

Dati motore
Potenza | 1.5 kW
Giri motore | 2500 rpm
Diametro albero | 19 mm

Successivamente, una volta trovato il numero di giri che vogliamo sviluppare sull’operatrice (n = 5000 rpm), calcolo il rapporto di trasmissione (i) e l’interasse
(I) tra i due elementi rotanti in base alla dimensione delle mie pulegge, che assumo a piacere dalla serie di Renard R20 a partire da un diametro minimo di 40 mm.
Assumiamo il diametro della puleggia motrice Dm = 100 mm e di conseguenza (per rispettare il rapporto di trasmissione e la serie R20) Do = 50 mm per il diametro dell’operatrice. Questa scelta `e giustificata dagli ingombri in fase di modellazione 3D per tagliare correttamente il tubo senza urti. Il calcolo dell’interasse dipende dal carico, nel nostro caso I ≥ 3 · Dm per trasmissioni a carico variabile. Una volta rispettata questa condizione si pu`o scegliere a piacimento la lunghezza in base alle esigenze (ingombri, etc...)
Dati Pulegge | Formula
Numero giri motrice (nm) | 2500 rpm | Fornito dal motore
Numero giri operatrice (no) | 5000 rpm | nm i
Rapporto di trasmissione (i) | 0.5 | nm no
Diametro puleggia motrice (Dm) | 100 mm | Scelta personale rispettando R20
Diametro puleggia operatrice (Do) | 50 mm | Do = Dm · i
Interasse (I) | 300 mm | I = 3 · Dm

7

Durante la progettazione di una trasmissione `e importante consultare le tabelle unificate che forniscono dati di correzione in base ai materiali utilizzati per la realizzazione e il servizio che devono compiere. Dati provenienti dalle tabelle del manuale di Meccanica:

Dati tabelle | Provenienza dati
Fs | 1.2 | Tab. I.101 Fattore di servizio
Ft | 1 | Tab. I.102 Fattore correttivo
Fα | 1 | Tab. I.108 Coeff. correzione
P1 | 0.7 | Tab. I.106 P specifica (cinghia gomma-tessile)

Calcolo della potenza corretta

Pc = P · Fs · Ft | (2.5)

Dove P `e la potenza erogata dal motore, Fs = 1.2 da tabella per macchine utensili che lavorano dalle 8 alle 10 ore al giorno e Ft = 1 da tabella per condizioni normali.
Pc = 1.5 kW · 1.2 · 1 = 1.8 kW | (2.6)

### 2.2.5 Calcolo della velocit`a periferica della puleggia mino-

re

V =

πDminnmin 60 000 | (2.7)

Dove Dmin = Do e nmin = no.

V =

π · 50 · 5000 60 000
= 13.1 m s⁻¹ | (2.8)

Calcolo della lunghezza della cinghia

l = 2I +

π(Dm + Do)
2

+

(Do − Dm)

2
4I

= 838 mm ≈ 840 mm (2.9)

Si approssima a 840 mm per lasciare un po’ di gioco prima di tendere o allentare la cinghia.

Calcolo dell’angolo di avvolgimento α

α = 180◦ − 57◦
·

Dm − Do I
= 190◦ | (2.10)

Il valore servir`a per trovare F α da tabella.

8

Calcolo della larghezza della cinghia a

I principali materiali utilizzati per la costruzione di cinghie piatte sono:

- cuoio;
- struttura composita di laminati plastici e gomme o resine;
- struttura composita di gomme e tessili;
- cotone, balata e altre fibre tessili vegetali;
- gomma o materiali plastici (per alte velocit`a).

Da questa informazione si pu`o calcolare la larghezza della cinghia ricavando il valore P1 in base al materiale scelto, nel nostro caso gomma-tessile pesante in cotone a 4 tele, data la seguente formula:

a =

Pc
P1Fα

=

1.8 cm
0.7 cm · 1
= 2.57 cm ≈ 26 mm | (2.11)

La larghezza della cinghia `e stata scelta in riferimento ai valori dati dalla serie R40, a partire dal valore minimo di 16 mm.

Calcolo dello spessore della cinghia s

Dalla seguente tabella ricavo lo spessore s della cinghia in base al materiale scelto in precedenza. In questo caso 6 mm.

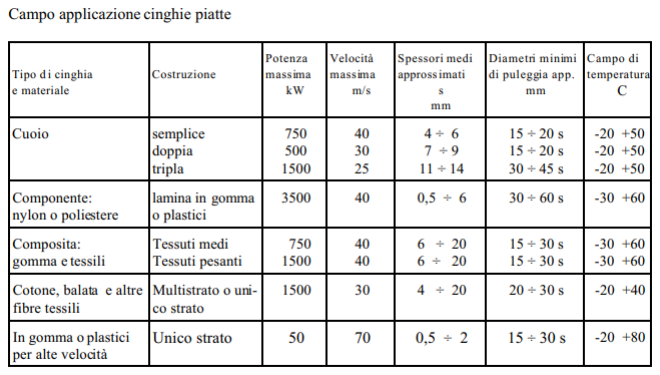
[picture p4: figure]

Figura 2.3: Parametri consigliati per vari tipi di cinghie

9

Calcolo della larghezza della puleggia b

b = a1.15 ≈ 30 mm | (2.12)

Calcolo della bombatura della puleggia h

Le pulegge per cinghie piatte vengono costruite con profilo esterno leggermente bombato per ottenere la stabilit`a della cinghia sulla corona. I materiali pi`u indicati sono l’alluminio, per il peso contenuto, o la ghisa per piccole serie.

h = b0.006 = 0.186 mm | (2.13)

## 2.3 Schema elettropneumatico

### 2.3.1 Scelta dei componenti

Lo schema elettropneumatico `e stato realizzato con i seguenti componenti:

Compressore Si occupa di accumulare e innalzare la pressione dell’aria all’interno del suo serbatoio per alimentare il circuito pneumatico;

Gruppo trattamento aria Composta da filtro di scarico manuale, un riduttore di pressione variabile, un manometro e una valvola di sicurezza (quasi sempre inclusa nei gruppi trattamento aria industriali per togliere aria al sistema in caso di emergenza);

Pistone pinza mobile 1M1, pistone pinza fissa 2M1, pistone espulsore 4M1 Composti dalla stessa logica, tramite l’uso di:

- 1 pistone a singolo effetto con ritorno a molla con le seguenti caratteristiche: corsa di 50 mm, diametro pistone 16 mm e forza di spinta teorica a 6 bar di F = 90 bar ÷ 120 bar (dove la sola andata `e utile per svolgere il lavoro richiesto di bloccaggio ed espulsione);
- 1 strozzatore che si utilizza solamente uno strozzatore senza una o pi`u valvole di non ritorno perch´e la regolazione della portata mediante strozzatura su ambedue i lati viene spesso applicata in cilindri a semplice effetto o in cilindri di piccole dimensioni che svolgono lavori “semplici”. Quest’aspetto inoltre va a vantaggio dei costi di realizzazione dell’impianto e della semplicit`a d’applicazione;
- 1 valvola 3/2 normalmente chiusa comandata elettricamente nella fase di spinta e con ritorno a molla;

Pistone sollevamento lama circolare 3MX Composto da:

- 1 pistone a doppio effetto con le seguenti caratteristiche: corsa 100 mm, diametro del pistone 32 mm e forza di spinta teorica a 6 bar di F = 415 N÷483 N, dati necessari a soddisfare il corretto movimento della lama verso l’alto, considerando che il peso che deve movimentare `e

10 composto dal telaietto con relativa trasmissione (motore, cinghia, pulegge etc) che risulta essere circa 25 kg, di conseguenza 250 N con un ulteriore aggiunta di 50 N per la fase di avanzamento come descritto nei calcoli. In questo modo, con una determinata forza richiesta (F = 300 N) `e stato scelto un pistone leggermente sovradimensionato per tenere conto delle possibili piccole perdite di forza dovute agli attriti dei perni a forcella;
- 2 strozzatori in scarico per ottenere una buona regolazione della portata, entro certi limiti indipendenti dal carico applicato allo stelo, poich´e viene guidato dal cuscino d’aria che si forma nella camera di scarico; agendo sulle viti di regolazione degli strozzatori si possono tarare separatamente le velocit`a delle due corse.
- 1 valvola 5/3 a centri chiusi comandata elettricamente con ritorno a molla in ambedue i versi di commutazione per comandare il pistone a doppio effetto. La scelta di questa valvola `e dovuta alla necessit`a di mantenere in posizione la lama (senza spostarsi in punti indesiderate, evitando danni all’oggetto da tagliare) in caso di arresto voluto o improvviso.

Finecorsa dei pistoni Festo prevede l’utilizzo di sensori magneti che determinano la corsa dello stelo, montati direttamente sul cilindro.

### 2.3.2 Lista componenti

Componenti | Quantit`a
Pistone sing. effetto | 3
Pistone doppio effetto | 1
Elettrovalvola 3/2 nc con ritorno a molla | 3
Elettrovalvola 5/3 centri chiusi con ritorno a molla | 1
Strozzatori | 5
Valvole di non ritorno | 2
Gruppo trattamento aria | 1
Compressore | 1

11

## 2.4 Elettronica

## 2.5 Programmazione

## 2.6 Utilizzo della macchina

## 2.7 Sviluppi futuri

## 2.8 Crediti

12

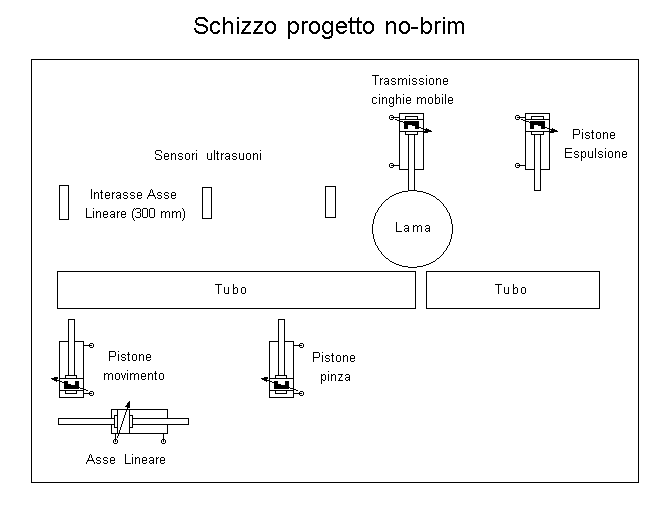
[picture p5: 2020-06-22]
Documentazione/src/img/schizzo_progetto.png

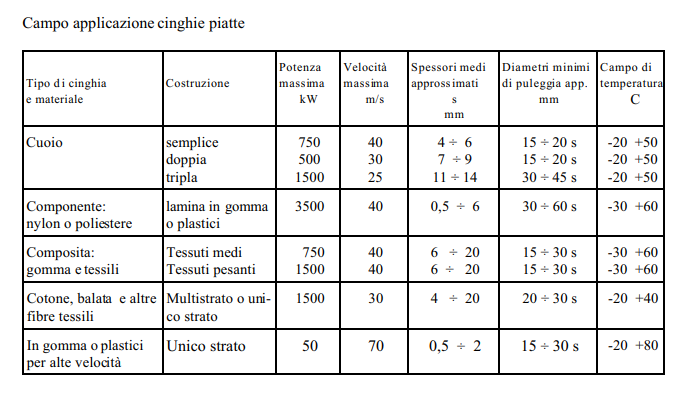
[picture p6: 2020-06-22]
Documentazione/src/img/tabella_cinghie.png

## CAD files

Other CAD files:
Quadro/Sinottico Cablaggio.dwg
Quadro/Copertina.dwg
Quadro/Schema Elettrico.dwg
Meccanica/Progetto Inventor no-brim/Assiemi/Assieme 1 - Trasporto.iam
Meccanica/Progetto Inventor no-brim/Assiemi/Assieme 2 - Taglio.iam
Meccanica/Progetto Inventor no-brim/Assiemi/Assieme completo - Trasporto Taglio.iam
Meccanica/Progetto Inventor no-brim/Assiemi/Lamiere e sensore ultrasuoni - Trasporto.iam
Meccanica/Progetto Inventor no-brim/Assiemi/Pistone scarico - Taglio.iam
Meccanica/Progetto Inventor no-brim/Assiemi/Pistoni pinza - Trasporto.iam
Meccanica/Progetto Inventor no-brim/Assiemi/Rulliera - Trasporto.iam
Meccanica/Progetto Inventor no-brim/Assiemi/Supporto saldato pistone 2 - Trasporto.iam
Meccanica/Progetto Inventor no-brim/Assiemi/Telaietto trasmissione - Taglio.iam
Meccanica/Progetto Inventor no-brim/Assiemi/Telaio - Taglio.iam
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

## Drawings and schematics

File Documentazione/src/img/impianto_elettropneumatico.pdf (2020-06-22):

## IMPIANTO ELETTROPNEUMATICO no-brim

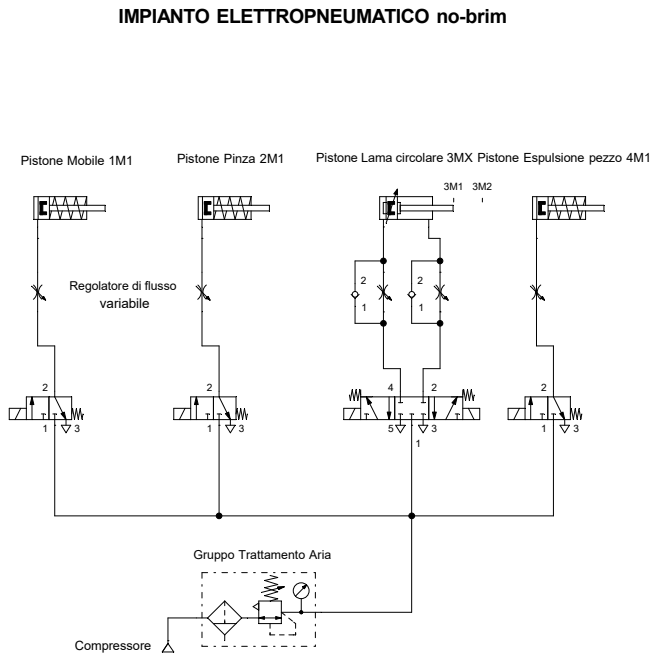
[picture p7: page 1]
Pistone Mobile 1M1; Pistone Pinza 2M1; Pistone Lama circolare 3MX Pistone Espulsione pezzo 4M1; Compressore

Regolatore di flusso
variabile

Gruppo Trattamento Aria

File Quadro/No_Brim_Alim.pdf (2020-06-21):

1 | 2 | 3 | 4 | 5 | 6 | 7 | 8 | 9 | 10
0 | 21/06/2020 | Utente DesignSpark Electrical | -X1 1

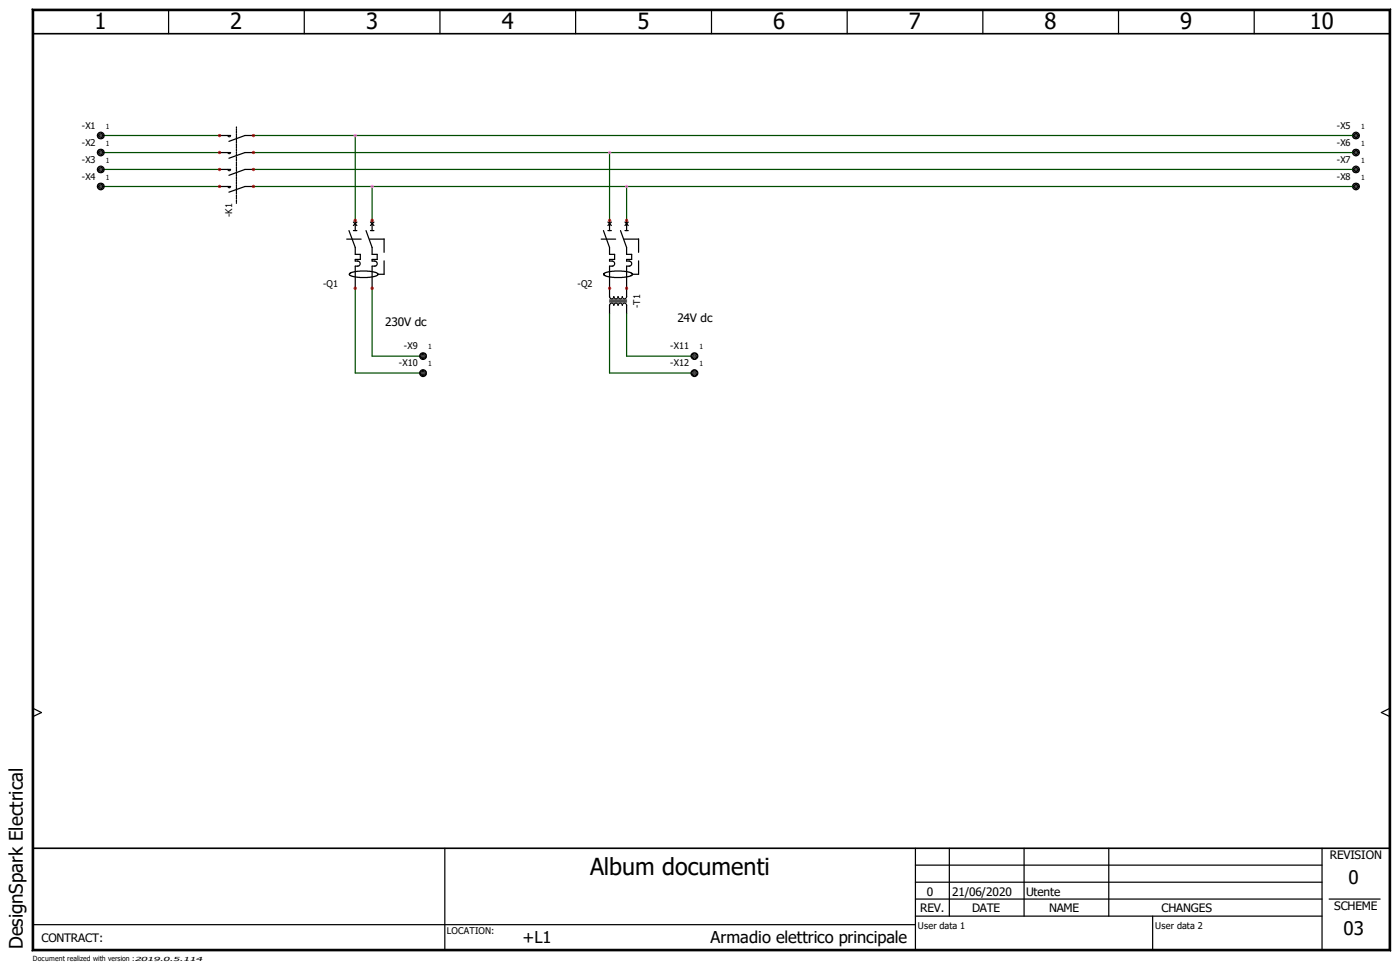
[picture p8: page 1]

Album documenti | REVISION 0 SCHEME

REV. | DATE | NAME | CHANGES

2019.0.5.114 | Armadio elettrico principale LOCATION: Document realized with version : CONTRACT:

User data 1 | User data 2 | 03 +L1

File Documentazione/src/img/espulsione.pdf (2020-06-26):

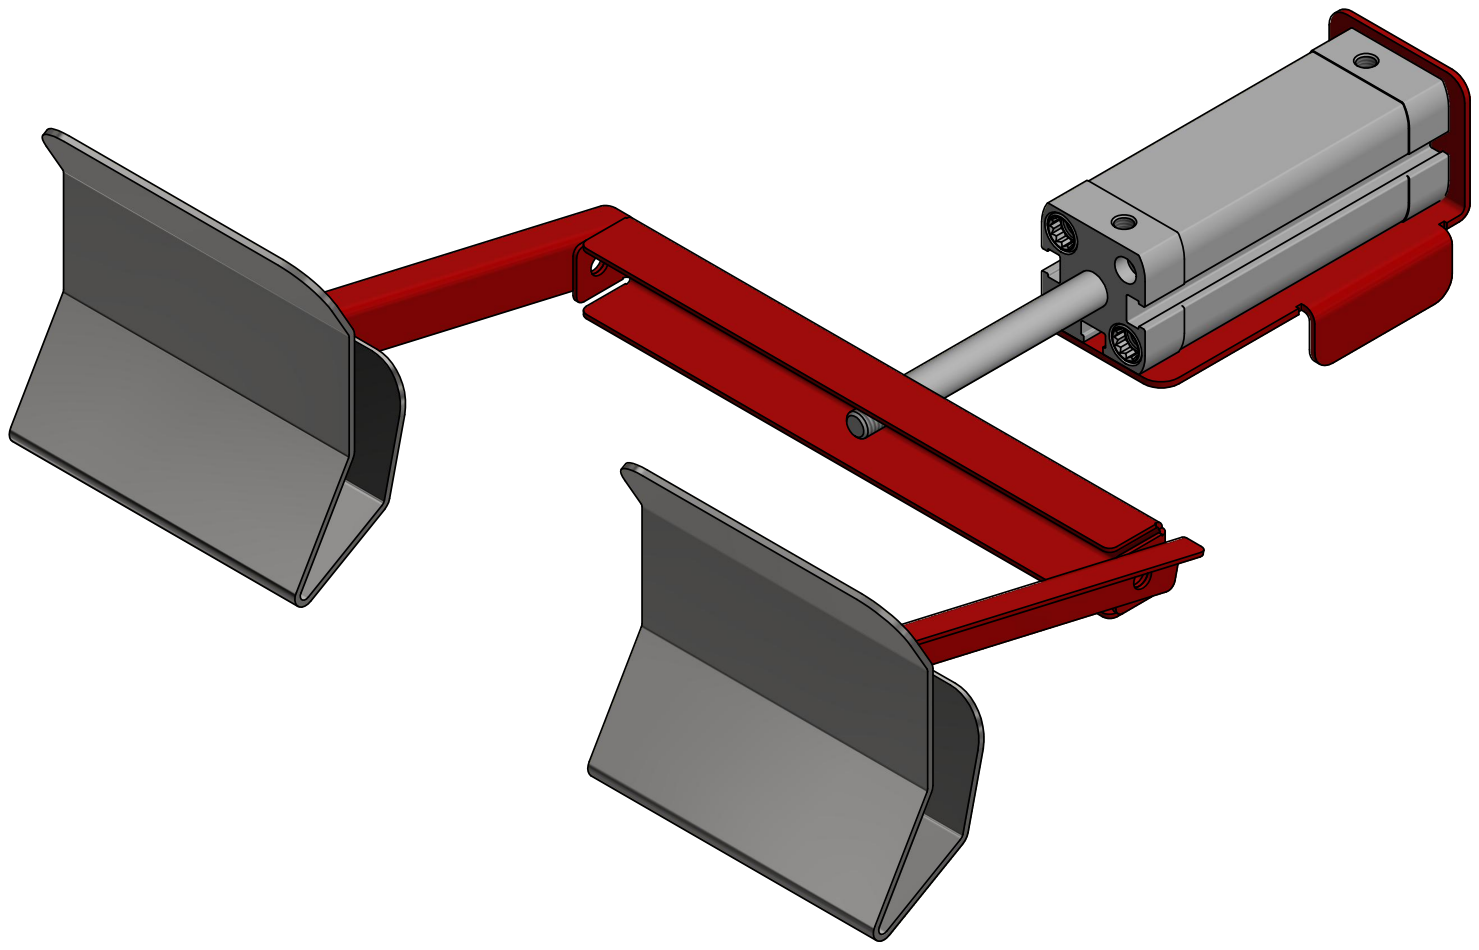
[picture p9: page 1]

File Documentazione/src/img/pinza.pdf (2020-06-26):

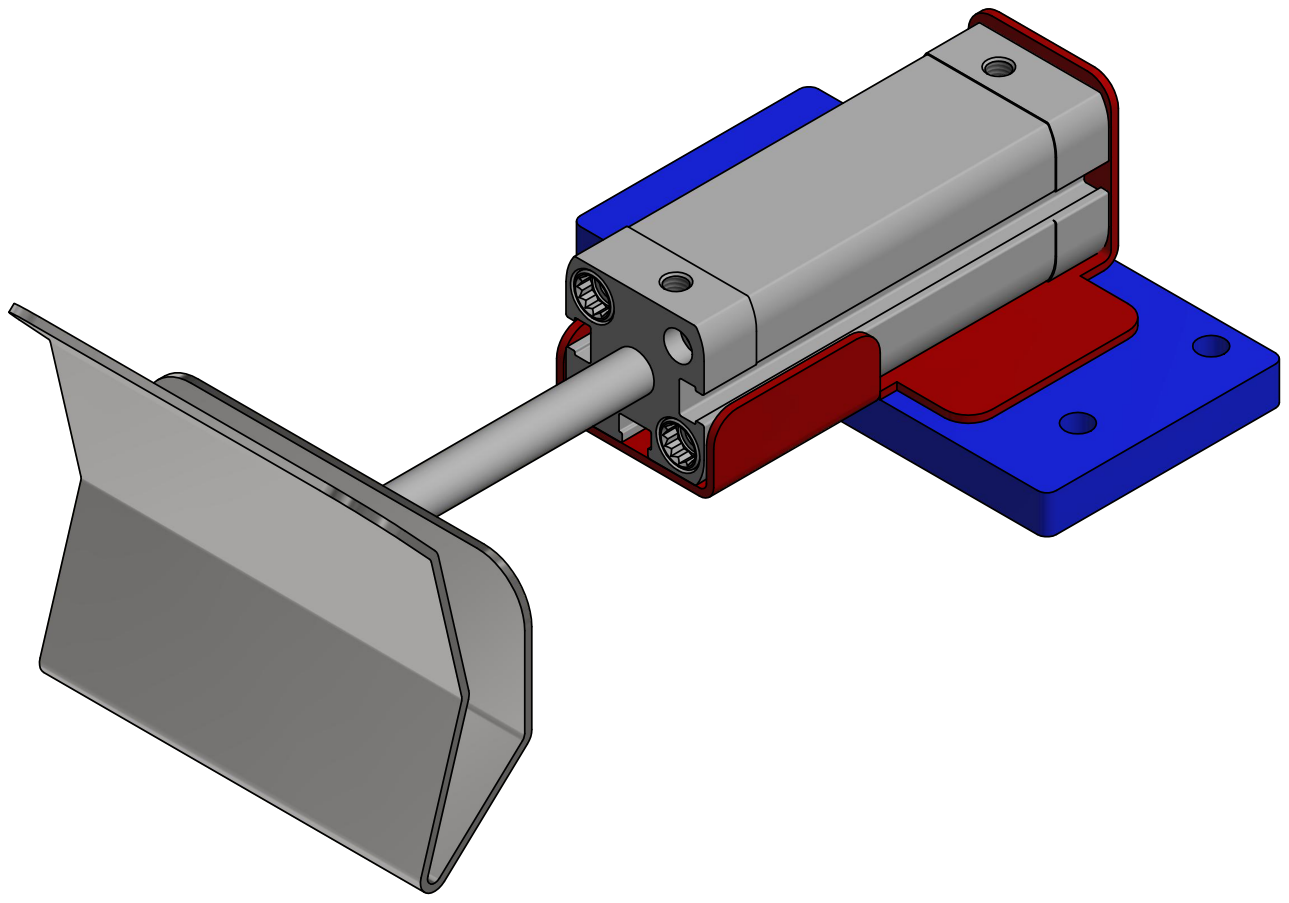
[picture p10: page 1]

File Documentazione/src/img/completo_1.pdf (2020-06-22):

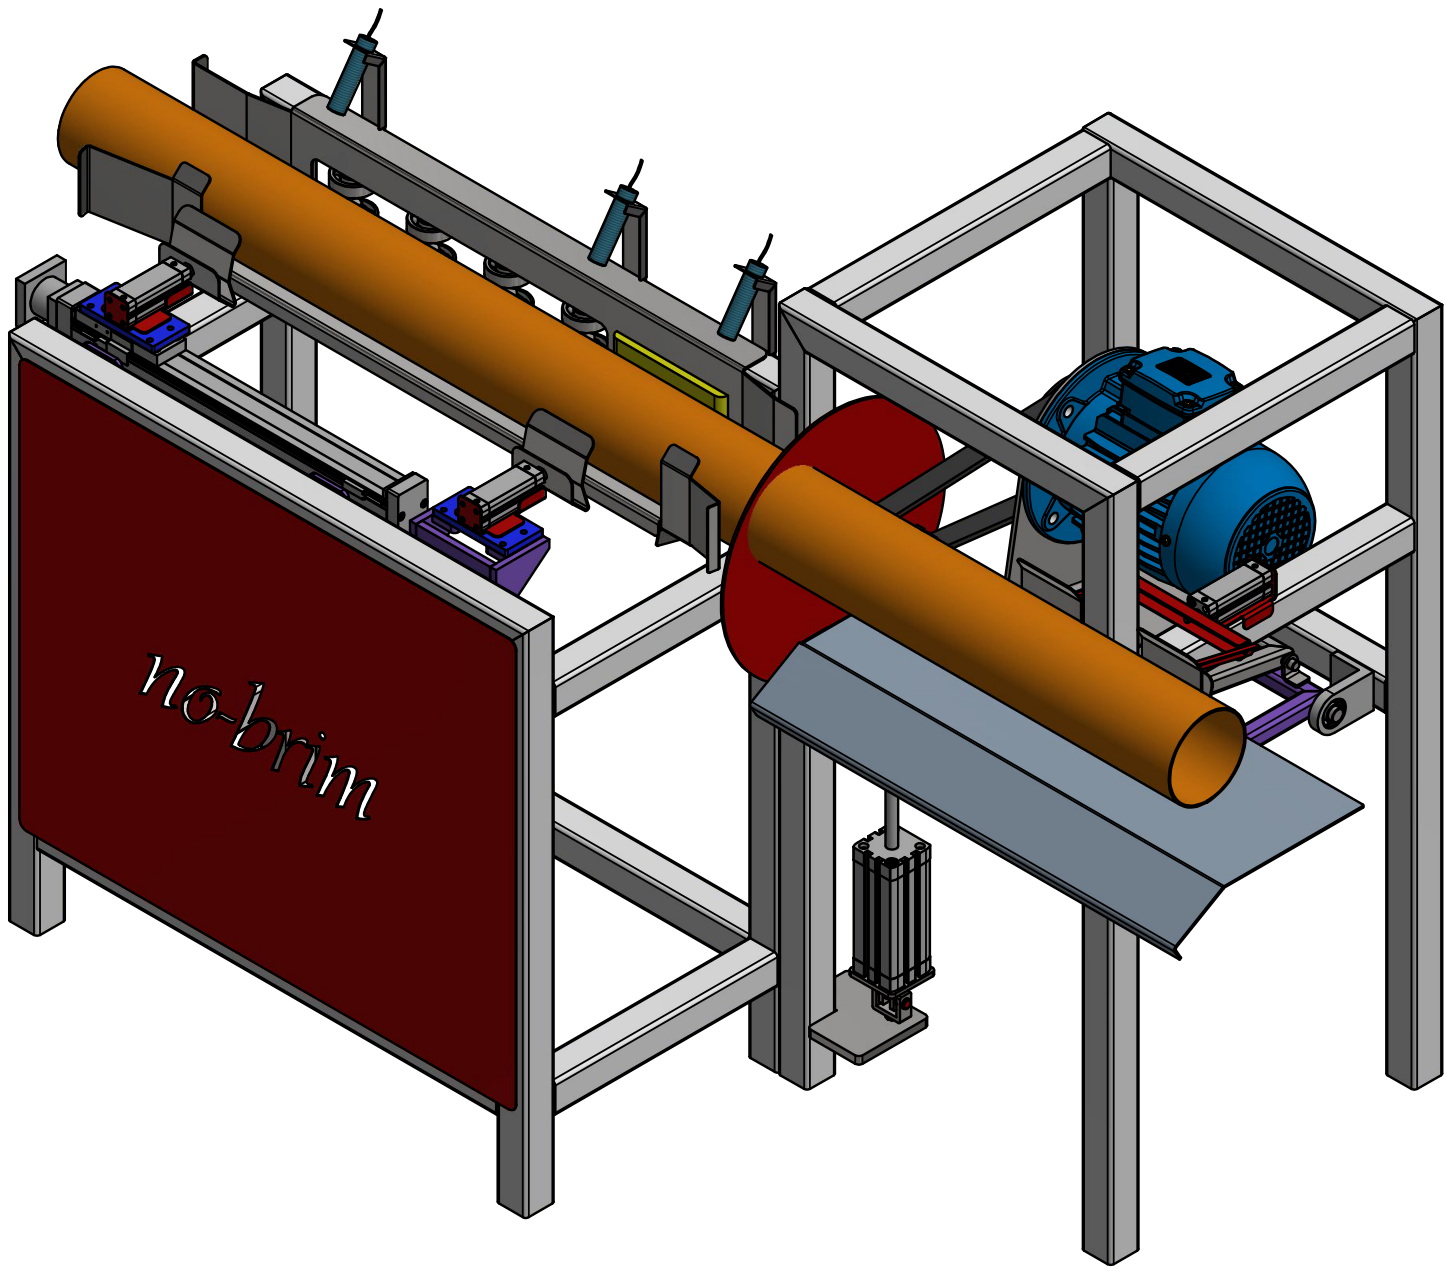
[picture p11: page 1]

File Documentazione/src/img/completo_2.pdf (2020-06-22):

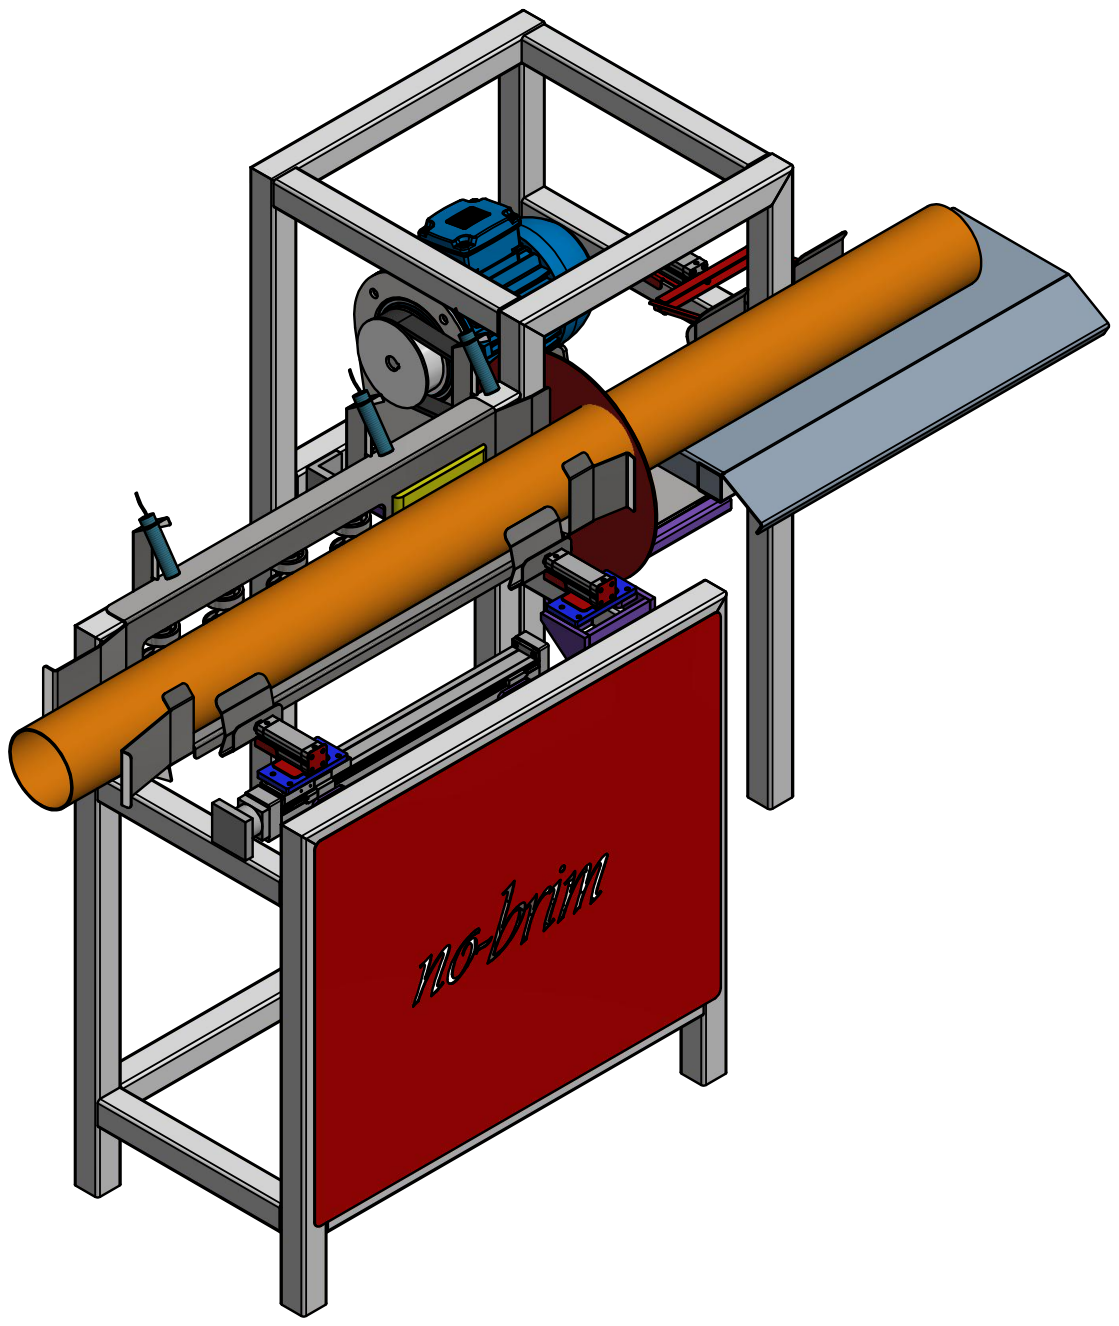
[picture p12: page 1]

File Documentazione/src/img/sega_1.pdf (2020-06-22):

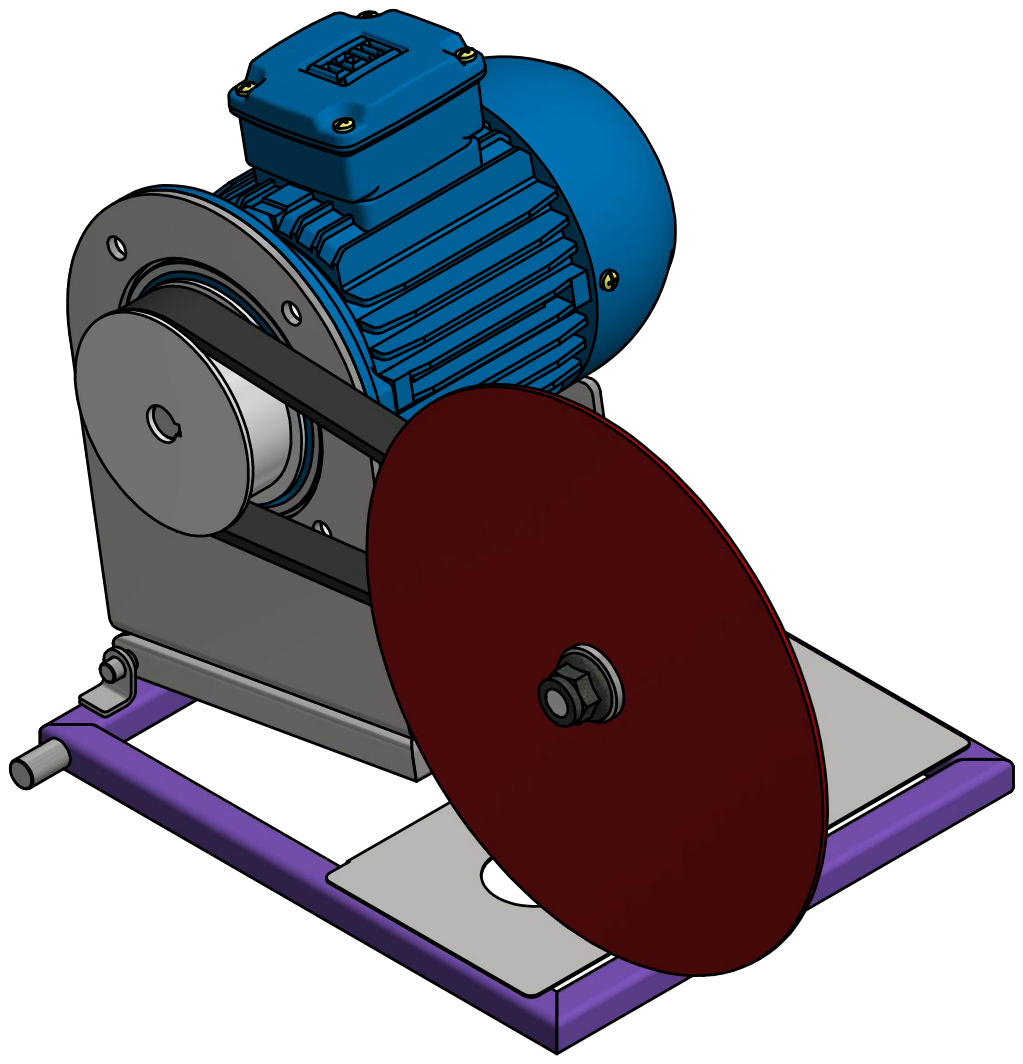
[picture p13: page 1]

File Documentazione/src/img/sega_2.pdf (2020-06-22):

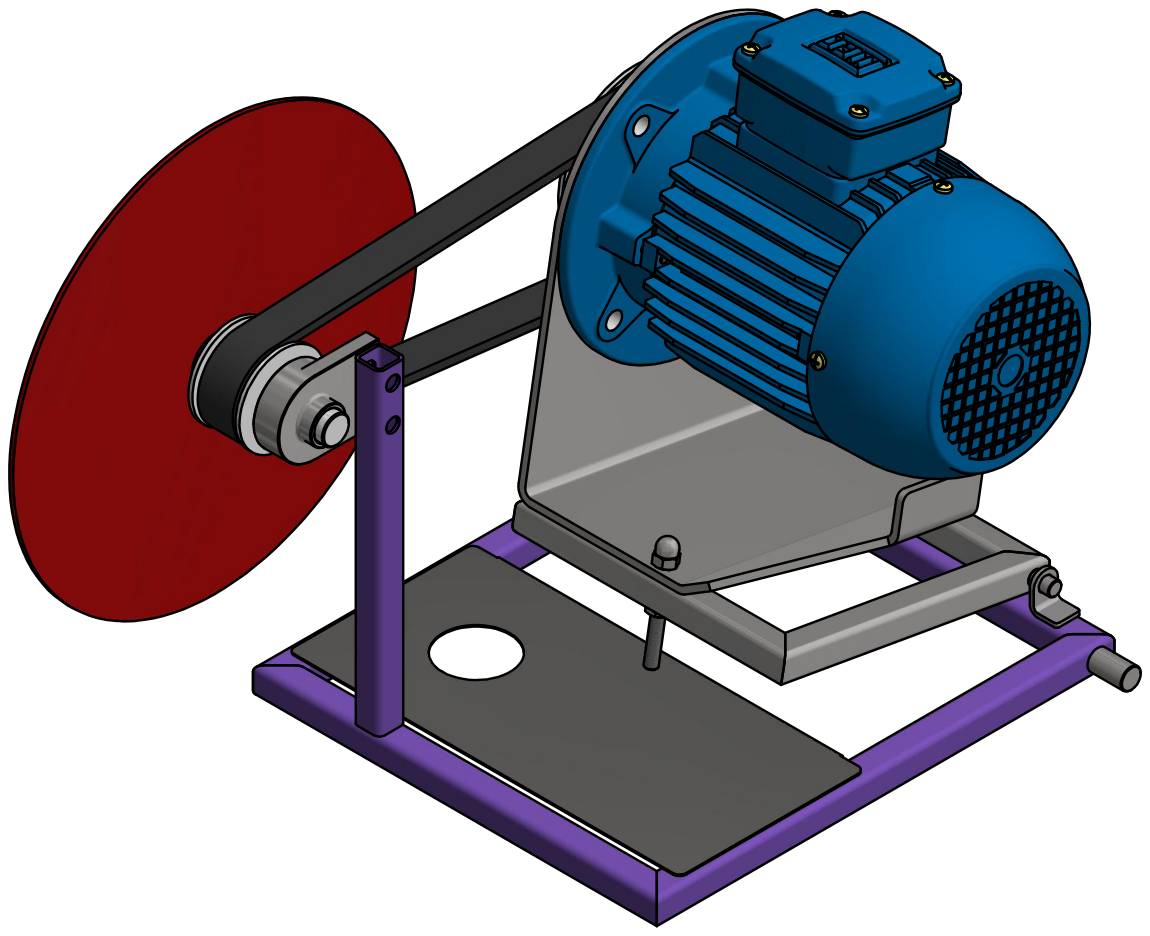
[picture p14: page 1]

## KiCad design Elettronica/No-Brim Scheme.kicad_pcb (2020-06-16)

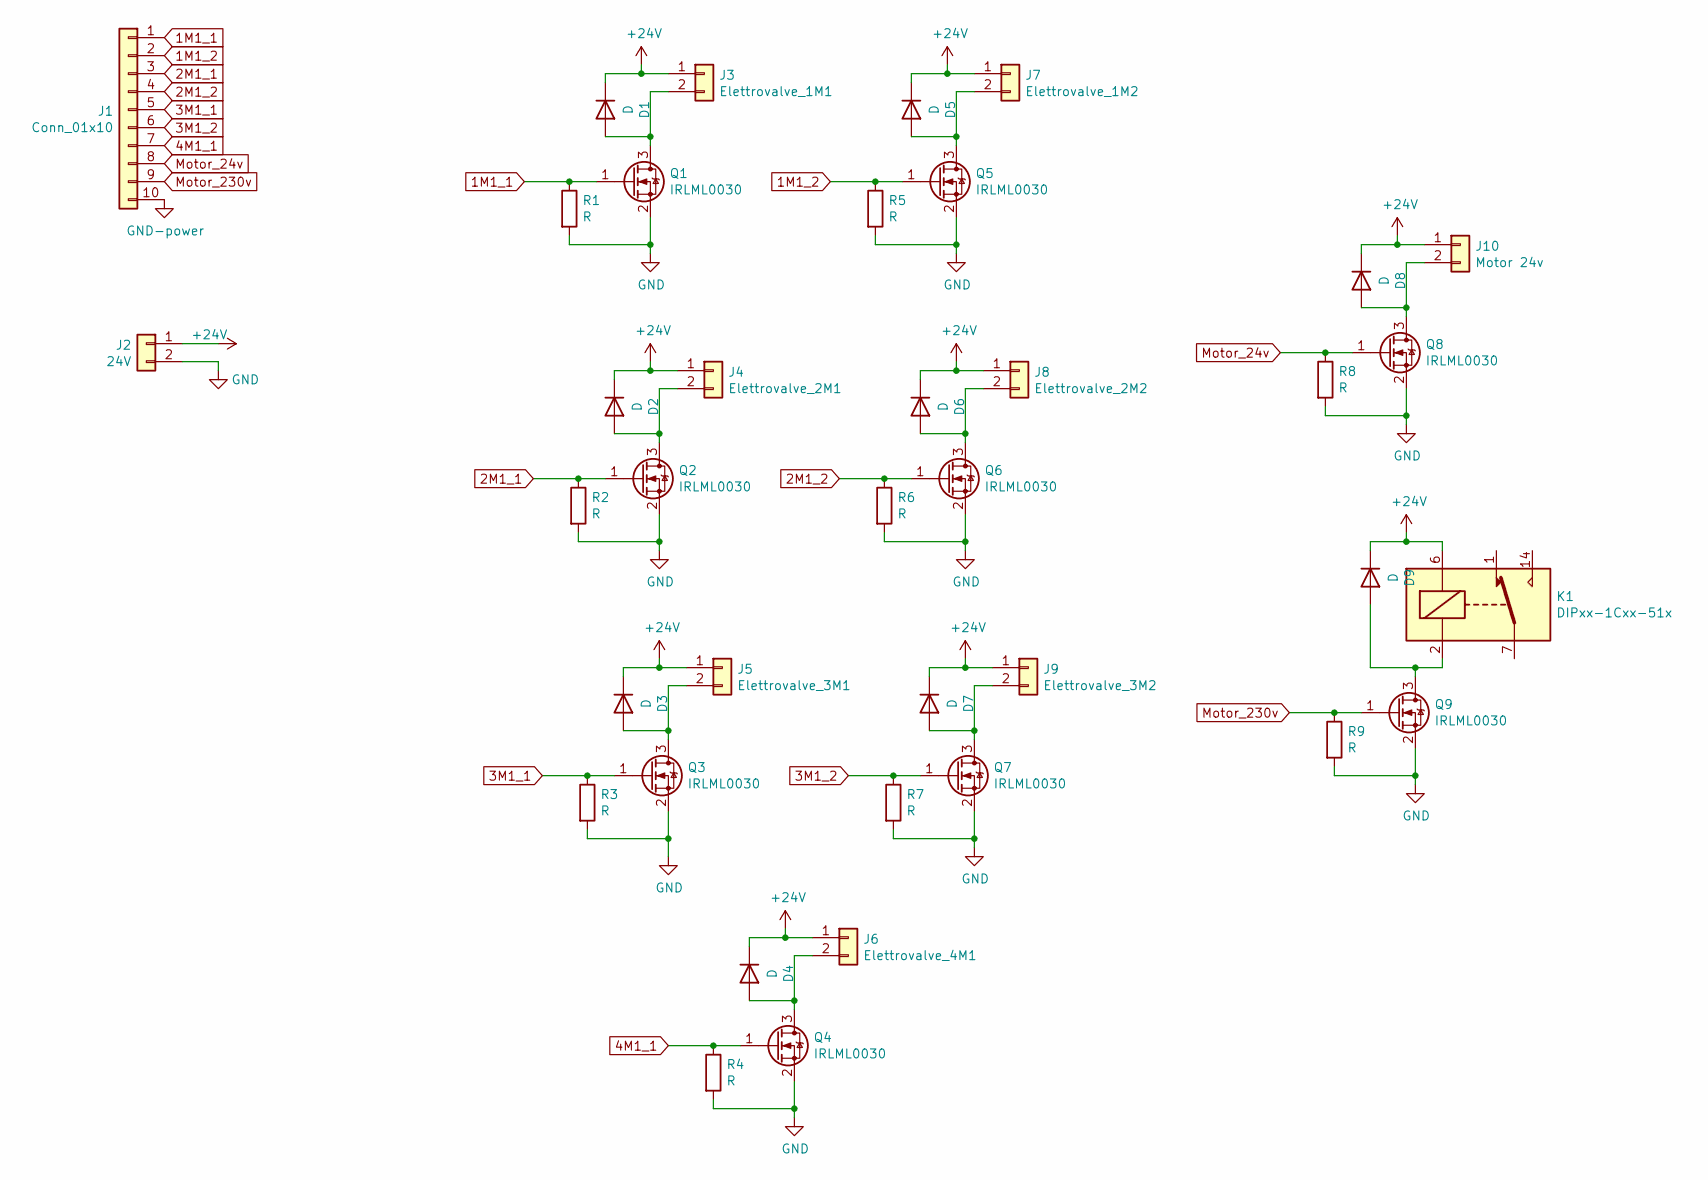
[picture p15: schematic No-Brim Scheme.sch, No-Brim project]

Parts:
D1, D2, D3, D4, D5, D6, D7, D8, D9: D; D_2010_5025Metric_Pad1.52x2.65mm_HandSolder
J1: Conn_01x10; PinSocket_1x10_P2.54mm_Vertical
J2: 24V; PinSocket_1x02_P2.00mm_Vertical
J3: Elettrovalve_1M1; PinSocket_1x02_P2.54mm_Vertical
J4: Elettrovalve_2M1; PinSocket_1x02_P2.54mm_Vertical
J5: Elettrovalve_3M1; PinSocket_1x02_P2.54mm_Vertical
J6: Elettrovalve_4M1; PinSocket_1x02_P2.54mm_Vertical
J7: Elettrovalve_1M2; PinSocket_1x02_P2.54mm_Vertical
J8: Elettrovalve_2M2; PinSocket_1x02_P2.54mm_Vertical
J9: Elettrovalve_3M2; PinSocket_1x02_P2.54mm_Vertical
J10: Motor 24v; PinSocket_1x02_P2.54mm_Vertical
K1: DIPxx-1Cxx-51x; Relay_StandexMeder_DIP_LowProfile
Q1, Q2, Q3, Q4, Q5, Q6, Q7, Q8, Q9: IRLML0030; SOT-23
R1, R2, R3, R4, R5, R6, R7, R8, R9: R; R_1206_3216Metric_Pad1.42x1.75mm_HandSolder

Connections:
1M1_1: J1.1, Q1.1 (G), R1.1
1M1_2: J1.2, Q5.1 (G), R5.1
2M1_1: J1.3, Q2.1 (G), R2.1
2M1_2: J1.4, Q6.1 (G), R6.1
3M1_1: J1.5, Q3.1 (G), R3.1
3M1_2: J1.6, Q7.1 (G), R7.1
4M1_1: J1.7, Q4.1 (G), R4.1
+24V: D1.1 (K), D2.1 (K), D3.1 (K), D4.1 (K), D5.1 (K), D6.1 (K), D7.1 (K), D8.1 (K), D9.1 (K), J2.1, J3.1, J4.1, J5.1, J6.1, J7.1, J8.1, J9.1, J10.1, K1.6
Motor_24v: J1.8, Q8.1 (G), R8.1
Motor_230v: J1.9, Q9.1 (G), R9.1
unnamed: D1.2 (A), J3.2, Q1.3 (D)
unnamed: D2.2 (A), J4.2, Q2.3 (D)
unnamed: D3.2 (A), J5.2, Q3.3 (D)
unnamed: D4.2 (A), J6.2, Q4.3 (D)
unnamed: D5.2 (A), J7.2, Q5.3 (D)
unnamed: D6.2 (A), J8.2, Q6.3 (D)
unnamed: D7.2 (A), J9.2, Q7.3 (D)
unnamed: D8.2 (A), J10.2, Q8.3 (D)
unnamed: D9.2 (A), K1.2, Q9.3 (D)
unnamed: K1.7, K1.8

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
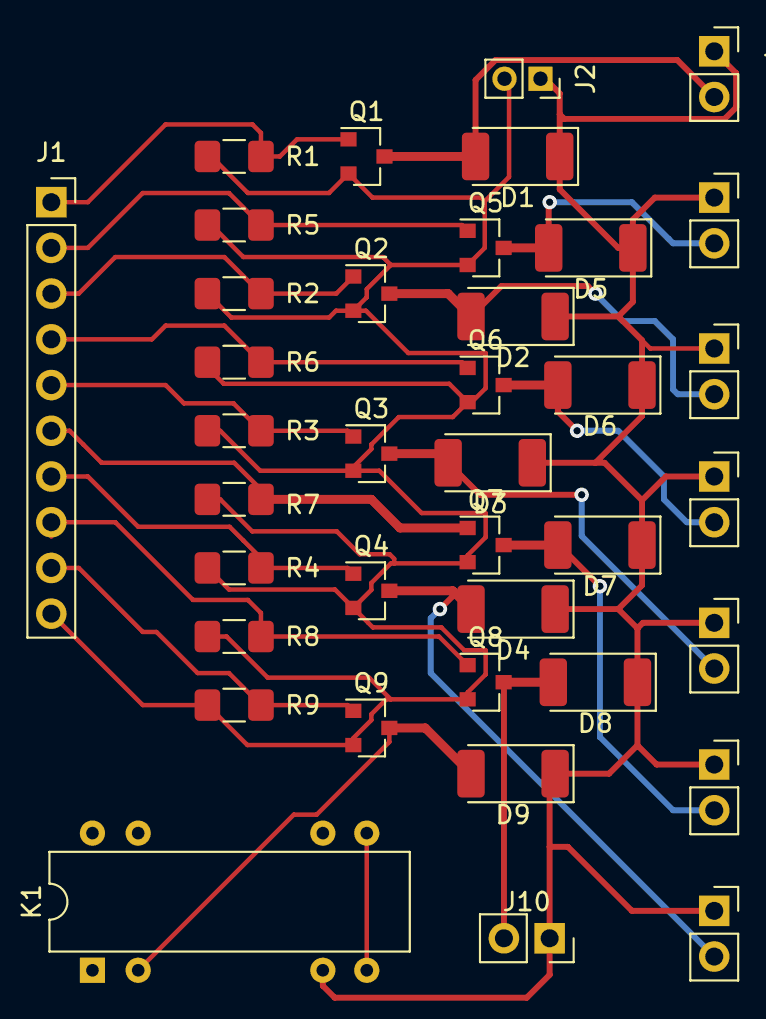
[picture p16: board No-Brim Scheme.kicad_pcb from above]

Board: 2 copper layers, 38 parts (0 on the bottom side), 21 nets.

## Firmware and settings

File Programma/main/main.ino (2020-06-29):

/*******************************
 * \mainpage no-brim
 * \section Introduzione
 * no-brim è il progetto di una macchina atta al taglio
 * automatico di tubi in PVC o altri materiali plastici.
 * \section Codice
 * Il codice è stato realizzato con un sistema a task, dove ogni
 * task esegue una funzione specifica come il controllo degli
 * I/O oppure del ciclogramma.
 *
 * \authors Daniele Moser <mailto:dnlmsr0@gmail.com>
 * \authors Francesco Maraner <mailto:francesco.maraner@marconirovereto.it>
 * \authors Michele Mattè <mailto:michele.matte@marconirovereto.it>
 *******************************/

#include "task.cpp"
#include "piston.cpp"
#include "CPUload.cpp"
#include "PID.cpp"

#define MAX_M1_VALUE 0 ///< Valore minimo asse lineare.
#define MIN_M1_VALUE 500 ///< Valore massimo asse lineare.

//Definizione input
#define I_1B1 2 ///< Finecorsa 1M1 retratto.
#define I_1B2 3 ///< Finecorsa 1M1 esteso.
#define I_2B1 4 ///< Finecorsa 2M1 retratto.
#define I_2B2 5 ///< Finecorsa 2M1 esteso.
#define I_3B1 6 ///< Finecorsa 3MX retratto.
#define I_3B2 7 ///< Finecorsa 3MX esteso.
#define I_4B1 8 ///< Finecorsa 4M1 retratto.
#define I_4B2 9 ///< Finecorsa 4M1 esteso.
#define I_B1 10 ///< Sensore di presenza B1.
#define I_B2 11 ///< Sensore di presenza B2.
#define I_B3 12 ///< Sensore di presenza B3.
#define I_EM1 13 ///< Encoder motore M1.
#define I_START 14 ///< Pulsante START.
#define I_STOP 15 ///< Pulsante STOP.
#define I_RESET 16 ///< Pulsante RESET.
#define I_EMG 17 ///< Pulsante di emergenza.

//Definizione output
#define O_1M1 18 ///< Output valvola 1M1.
#define O_2M1 19 ///< Output valvola 2M1.
#define O_3M1 20 ///< Output valvola 3M1.
#define O_3M2 21 ///< Output valvola 3M2.
#define O_4M1 22 ///< Output valvola 4M1.
#define O_M1 23 ///< Output motore asse lineare M1.
#define O_M2 24 ///< Output motore lama M2.

//Definizione variabili globali
int SFCstate; ///< Variabile di stato del sistema.
int SFCerror; ///< Variabile errore del sistema.
int V_EM1; ///< Valore encoder motore M1.
int cuttingMeasure; ///< Misura taglio del tubo.
int cuttingRemaining; ///< Rimanenza spostamento del tubo.

/// Lista dei task.
enum taskIndex {
                TASK_INTEGRITY, ///< Task per verificare l'integrità del sistema.
                TASK_PID, ///< Task di calcolo del PID.
                TASK_SFC, ///< Task del programma SFC.
                TASK_UI, ///< Task dell'interfaccia utente per il controllo.
                TASK_SERIAL, ///< Task gestione della seriale.
                TASK_MAX,
};

/// Lista dei pistoni.
enum pistonIndex {
                  PIST_1M1,
                  PIST_2M1,
                  PIST_3MX,
                  PIST_4M1,
                  PIST_MAX,
};

/// Lista degli stati SFC.
enum SFCstates {
                SFC_EMERGENCY,
                SFC_STOP,
                SFC_CALIBRATION,
                SFC_MOVE_PREP,
                SFC_MOVE_FRONT,
                SFC_MOVE_BACK,
                SFC_STOP_TUBE,
                SFC_CUT,
                SFC_STOP_CUT,
                SFC_EXPULSION,
                SFC_END_EXPULSION,
};

struct TaskStruct tasks[TASK_MAX]; ///< Vettore dei task.
struct measureTimingStruct measureTiming; ///< Oggetto misura delle tempistiche.
struct PistonStruct pistons[PIST_MAX]; ///< Vettore dei pistoni.
struct PID PIDasse; ///< Oggeto PID.

int function_taskIntegrity(void);
int function_taskPID(void);
int function_taskSFC(void);
int function_taskUI(void);
int function_taskSerial(void);

void setup () {
  tasks[TASK_INTEGRITY].init(20);
  tasks[TASK_PID].init(20);
  tasks[TASK_SFC].init(20);
  tasks[TASK_UI].init(20);
  tasks[TASK_SERIAL].init(10);

  PIDasse.init(1,1,1,255,0);
  Serial.begin(38400);

  SFCstate = 0;

  //Iinizializzazione I/O.
  pinMode(2, INPUT);
  pinMode(3, INPUT);
  pinMode(4, INPUT);
  pinMode(5, INPUT);
  pinMode(6, INPUT);
  pinMode(7, INPUT);
  pinMode(8, INPUT);
  pinMode(9, INPUT);
  pinMode(10, INPUT);
  pinMode(11, INPUT);
  pinMode(12, INPUT);
  pinMode(13, INPUT);
  pinMode(14, INPUT);
  pinMode(15, INPUT);
  pinMode(16, INPUT);
  pinMode(17, INPUT);

  pinMode(18, OUTPUT);
  pinMode(19, OUTPUT);
  pinMode(20, OUTPUT);
  pinMode(21, OUTPUT);
  pinMode(22, OUTPUT);
  pinMode(23, OUTPUT);
  pinMode(24, OUTPUT);

  //Inizializzazione pistoni.
  pistons[PIST_1M1].init(O_1M1,0,I_1B2,I_1B1);
  pistons[PIST_2M1].init(O_2M1,0,I_2B2,I_2B1);
  pistons[PIST_3MX].init(O_3M1,O_3M2,I_3B1,I_3B2);
  pistons[PIST_4M1].init(O_4M1,0,I_4B1,I_4B2);

  cuttingMeasure = 750;
  cuttingRemaining = cuttingMeasure;
}


void loop () {

  measureTiming.startMeasure(micros());

  long timeNow = millis();

  if (tasks[TASK_INTEGRITY].toDoTask(timeNow)) function_taskIntegrity();
  if (tasks[TASK_PID].toDoTask(timeNow)) function_taskPID();
  if (tasks[TASK_SFC].toDoTask(timeNow)) function_taskSFC();
  if (tasks[TASK_UI].toDoTask(timeNow)) function_taskUI();
  if (tasks[TASK_SERIAL].toDoTask(timeNow)) function_taskSerial();

  measureTiming.endMeasure(micros());
}

int function_taskIntegrity () {}
int function_taskPID () {}

/**Funzione degli stati macchina (SFC).
 *La funzione contiene il programma della macchina
 *in un codice che descrive i vari stati e le transizioni
 */
int function_taskSFC () {
  switch(SFCstate){

    /**Stato di emergenza.
     *Tutti i pistoni sono spenti. La transizione richiede
     *la pressione del pulsante RESET per passare allo
     *stato di stop.
     */
  case SFC_EMERGENCY:
    for(byte i = 0; i<PIST_MAX; i++) pistons[i].off();
    if (digitalRead(I_RESET)){
      SFCstate=SFC_STOP;
      SFCerror=0;
    }
    break;

    /**Stato di stop.
     *Tutti i pistoni sono spenti. La transizione richiede
     *la pressione del pulsante START per passare allo stato
     *di calibrazione della macchina.
     */
  case SFC_STOP:
    for(byte i = 0; i<PIST_MAX; i++) pistons[i].off();
    if (digitalRead(I_START)){
      SFCstate=SFC_CALIBRATION;
      SFCerror=0;

      int movingMeasure;
      if (cuttingRemaining >= MAX_M1_VALUE) movingMeasure = MAX_M1_VALUE;
      else movingMeasure = cuttingRemaining;
      cuttingRemaining -= movingMeasure;
      PIDasse.setSetPoint(MAX_M1_VALUE);
    }
    break;

    /** Stato di calibrazione.
     * La macchina viene calbrata, ovvero 1M1 e 3MX si ritraggono,
     * mentre 2M1 e 4M1 si estendono. L'asse lineare si sposta
     * nella posizione più lontana dalla lama. La transizione
     * richiede che tutte le movimentazioni siano in posizione per
     * passare allo stato di preparazione alla movimentazione.
     */
  case SFC_CALIBRATION:
    pistons[PIST_2M1].extend();
    pistons[PIST_1M1].retract();
    pistons[PIST_3MX].retract();
    pistons[PIST_4M1].retract();
    analogWrite(O_M1, PIDasse.compute(V_EM1,millis()));
    if (pistons[PIST_2M1].extensionState && pistons[PIST_1M1].retractionState && pistons[PIST_3MX].retractionState && pistons[PIST_4M1].retractionState && PIDasse.setPointReached){
      SFCstate = SFC_MOVE_PREP;
    }
    break;

    /** Stato preparazione movimentazione.
     * Il pistone 1M1 si estende mentre il pistone 2M1 si ritrae.
     * La transizione richiede che la pinza movimentata sia in posizione.
     */
  case SFC_MOVE_PREP:
    pistons[PIST_1M1].extend();
    if (pistons[PIST_1M1].extensionState){
      SFCstate=SFC_MOVE_FRONT;
      PIDasse.setSetPoint(MIN_M1_VALUE);
    }
    break;

    /** Stato movimentazione in avanti.
     * L'asse si muove verso la lama fino a raggiungere
     * la fine della sua corsa.
     */
  case SFC_MOVE_FRONT:
    pistons[PIST_2M1].retract();
    analogWrite(O_M1, PIDasse.compute(V_EM1,millis()));
    if (pistons[PIST_2M1].retractionState && PIDasse.setPointReached){
      SFCstate=SFC_STOP_TUBE;
    }
    break;

    /** Stato blocco del tubo.
     * Viene bloccato il tubo tramite il pistone 2M1.
     */
  case SFC_STOP_TUBE:
    pistons[PIST_2M1].extend();
    if (pistons[PIST_2M1].extensionState){
      if (cuttingRemaining == 0) SFCstate= SFC_CUT;
      else {
        int movingMeasure;
        if (cuttingRemaining >= MAX_M1_VALUE) movingMeasure = MAX_M1_VALUE;
        else movingMeasure = cuttingRemaining;
        cuttingRemaining -= movingMeasure;
        PIDasse.setSetPoint(movingMeasure);
        SFCstate=SFC_CALIBRATION;
      }
    }
    break;

    /** Stato taglio del tubo.
     * Il tubo viene tagliato con il motore lama M2 e il
     * pistone 3MX. La transizione richiede il taglio completo
     * del tubo, ovvero che il pistone 3MX raggiunga la fine
     * della sua corsa.
     */
  case SFC_CUT:
    digitalWrite(O_M2,1);
    pistons[PIST_3MX].extend();
    if(pistons[PIST_3MX].extensionState){
      digitalWrite(O_M2,0);
      SFCstate=SFC_STOP_CUT;
    }
    break;

    /** Stato fine taglio.
     * La lama viene fermata e il pistone 3MX si ritrae.
     * La transizione richiede che il pistone 3MX raggiunga
     * la fine della sua corsa.
     */
  case SFC_STOP_CUT:
    digitalWrite(O_M2,0);
    pistons[PIST_3MX].retract();
    if(pistons[PIST_3MX].retractionState){
      SFCstate=SFC_EXPULSION;
    }
    break;

    /** Stato espulsione pezzo.
     * Il pezzo viene espulso tramite il pistone 4M1.
     * La transizione richiede che il pistone 4M1 torni
     * a riposo.
     */
  case SFC_EXPULSION:
    pistons[PIST_4M1].extend();
    if(pistons[PIST_4M1].extensionState)SFCstate=SFC_END_EXPULSION;
  break;

  /** Stato fine espulsione pezzo.
   * Il pezzo è stato espulso e 4M1 torna a riposo
   */
  case SFC_END_EXPULSION:
    pistons[PIST_4M1].retract();
    if(pistons[PIST_4M1].retractionState)SFCstate=SFC_CALIBRATION;
    break;
  }
}


int function_taskUI () {}
int function_taskSerial () {}

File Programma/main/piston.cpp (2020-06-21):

#include <Arduino.h>
/**Struttura pisotni
 * La struttura definisce tutte le funzioni necessarie per
 * il corretto funzionamento dei pistoni.
 * Viene utilizzato un sistema di variabili per input e output
 * sulle quali verranno rispettivamente scritti i valori
 * in ingresso e letti i valori delle uscite,
 * questo per non sovraccaricare il sistema ogni volta che
 * si richiama la funzione digitalWrite o digitalRead.
 */
struct PistonStruct {
  int extensionPin;         ///< Pin OUTPUT estensione
  int retractionPin;        ///< Pin OUTPUT ritrazione
  int extensionFC;          ///< Fine corsa posizione estenso
  int retractionFC;         ///< Fine corsa posizione ritratto
  bool retractionState;  ///< Verifica finecorsa posizione ritratto
  bool extensionState;   ///< Verifica finecorsa posizione esteso
  bool ext;              ///< Stato uscita estensione pistone
  bool ret;              ///< Stato uscita ritrazione pistone


  /**Inizializza variabili.
   * La funzione inizializza le principali variabili come
   * i pin di INPUT e OUTPUT.
   * \param ExtensionPin Pin OUTPUT per estensione pistone.
   * \param RetractionPin Pin OUTPUT per ritrazione pistone.
   * \param ExtensionFC Pin INPUT del finecorsa posizione esteso.
   * \param RetractionFC Pin INPUT del finecorsa posizione ritratto.
   */
  void init (int ExtensionPin, int RetractionPin, int ExtensionFC, int RetractionFC) { //
    extensionPin = ExtensionPin;
    extensionFC = ExtensionFC;
    retractionFC = RetractionFC;
    retractionPin = RetractionPin;

    pinMode (extensionPin, OUTPUT);
    pinMode (retractionPin, OUTPUT);
    pinMode (extensionFC, INPUT);
    pinMode (retractionFC, INPUT);
  }


  /**Lettura ingressi.
   * La funzione richiama due `digitalRead()` per la lettura
   * dei due finecorsa relativi al pistone.
   */
  void read() {
    extensionState = digitalRead(extensionFC);
    if (retractionPin)retractionState = digitalRead(retractionFC);
    else retractionState = !extensionState;
  }

  /**Scrittura uscite.
   * La funzione richiama due `digitalWrite()` per la scrittura
   * delle due uscite relative al pistone. Nel caso in cui si
   * tratti di un pistone monostabile, viene ignorato il pin
   * di ritrazione.
   */
  void write() {
    digitalWrite(extensionPin, ext);
    if (retractionPin) digitalWrite(retractionPin, ret);
  }


  /**Spegne tutte le uscite.
   * Spegne tutte le uscite del pistone. Nel caso di un pistone
   * monostabile, questo ritorna alla sua posizione di riposo.
   */
  void off() {
    ext = 0;
    ret = 0;
  }


  /**Scrittura variabili per estensione.
   * Scrittura variabili per la corretta esecuzione di
   * un'estensione. Non viene direttamente cambiato l'OUTPUT
   * in quanto questo viene eseguito nella funzione @ref write.
   */
  void extend() {
    ext = 1;
    ret = 0;
  }


  /**Scrittura variabili per ritrazione.
   * Scrittura variabili per la corretta esecuzione di
   * una ritrazione. Non viene direttamente cambiato l'OUTPUT
   * in quanto questo viene eseguito nella funzione @ref write.
   */
  void retract() {
    ext = 0;
    ret = 1;
  }
};

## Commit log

2020-05-29 prima parte macchina no brim
    [536218 ADN-50-P---(Z).ipt, 536218 ADN-50-P-A_(KS).ipt, 536331 ADN-16-50-A-P-A---(asm_0).iam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]
2020-05-29 Organizzata repository
    [536218 ADN-50-P---(Z).ipt, 536218 ADN-50-P-A_(KS).ipt, 536331 ADN-16-50-A-P-A---(asm_0).iam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]
2020-05-30 Ricreato progetto
    [536218 ADN-50-P---(Z).ipt, 536218 ADN-50-P-A_(KS).ipt, 536331 ADN-16-50-A-P-A---(asm_0).iam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]
2020-05-30 Nuovo schizzo Trasporto
    [536218 ADN-50-P---(Z).ipt, 536218 ADN-50-P-A_(KS).ipt, 536331 ADN-16-50-A-P-A---(asm_0).iam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]
2020-06-01 Quasi completato trasporto, iniziata la parte di taglio
    [536331 ADN-16-50-A-P-A---(asm_0).iam, Appoggio pistone supp.saldato.ipt, Assieme 1 - Trasporto.iam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]
2020-06-03 Lista componenti principali
    [BOM.csv]
2020-06-03 Modifiche parte trasporto
    [536331 ADN-16-50-A-P-A---(asm_0).iam, Albero cuscinetto.ipt, Assieme 1 - Trasporto.iam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]
2020-06-05 Modifiche trasmissione e telaietto
    [Assieme 1 - Trasporto.iam, Assieme 2 - Taglio.iam, Assieme completo - Trasporto Taglio.iam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]
2020-06-10 Create task e scheduler
    [BOM.csv]
2020-06-10 Schema 10/6
    [No-Brim Scheme.kicad_pcb, No-Brim Scheme.sch]
2020-06-11 Aggiunte Eletrovalvole mancanti
    [BOM.csv]
2020-06-12 Aggiunta pistone salita lama e modifiche varie
    [536288 ADN-100-P---(Z).ipt, 536288 ADN-100-P-I_(KS).ipt, 536288 ADN-40-100-I-P-A---(0).iam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]
2020-06-15 Integrazione funzionalità PID
2020-06-15 Aggiustata BOM
    [BOM.csv]
2020-06-16 Modifiche allo schema e pcb recuperato(16/6)
    [No-Brim Scheme.kicad_pcb, No-Brim Scheme.sch]
2020-06-16 PCB completato da revisionare(16/6)
    [No-Brim Scheme.kicad_pcb, No-Brim Scheme.sch]
2020-06-16 Progetto quasi finito
    [536288 ADN-40-100-I-P-A---(0).iam, 536331 ADN-16-50-A-P-A---(asm_0).iam, Albero cuscinetto.ipt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]
2020-06-19 Modificato PID
2020-06-19 Aggiunto Asse lineare e motore annesso
    [BOM.csv]
2020-06-21 Alimentazione 230v & 24v
    [Copertina.dwg, Schema Elettrico.dwg, Sinottico Cablaggio.dwg]
2020-06-21 Modifiche alla scaletta + Disegni quadro spostati
    [Copertina.dwg, Schema Elettrico.dwg, Sinottico Cablaggio.dwg]
2020-06-22 Parte Inventor finita, primi PDF e documentazione meccanica
    [536288 ADN-40-100-I-P-A---(0).iam, Assieme 1 - Trasporto.iam, Assieme 1 - Trasporto.idw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]
2020-06-24 Modificata BOM
    [BOM.csv]
2020-06-25 Modificata documentazione di meccanica
2020-06-26 2 pdf pistoni
    [536331 ADN-16-50-A-P-A---(asm_0).iam, Pistone scarico - Taglio.iam]
